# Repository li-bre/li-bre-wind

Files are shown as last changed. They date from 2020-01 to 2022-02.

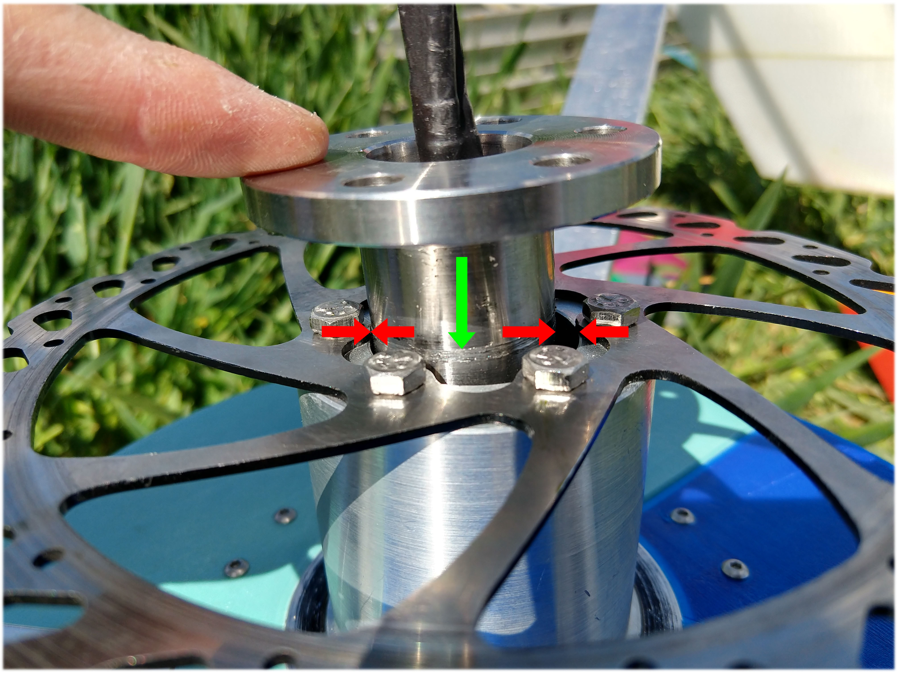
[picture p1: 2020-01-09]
05_Photos/02_Construction/01 Rotor/IMG_20190512_130845734_HDR.jpg

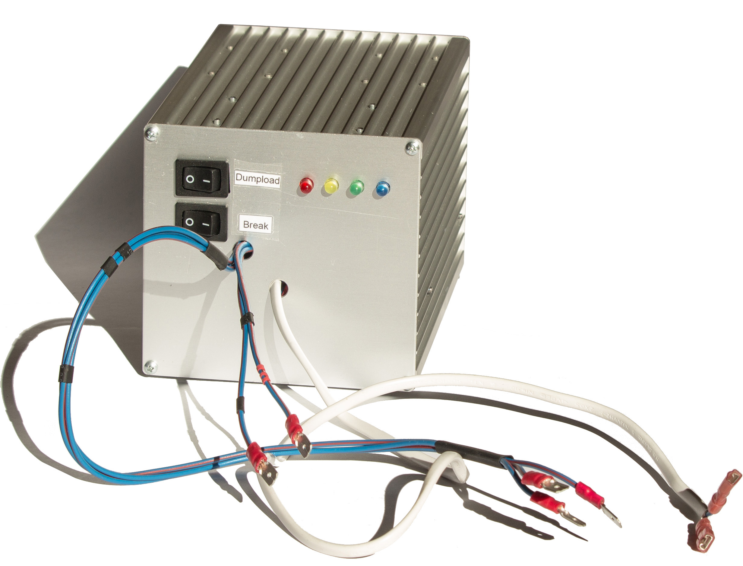
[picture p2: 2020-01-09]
05_Photos/02_Construction/02 Control/Control_Unit_closed.jpg

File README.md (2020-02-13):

# Li.Bre wind

**Li.Bre wind** is a project by [Avia Linke](https://github.com/a-linke) and [Julian Brendel](https://github.com/j-brendel) that offers an open source solution for an micro off-grid system powered by a 3D printed helical darrieus wind turbine. The project was developed as a master thesis at Technische Universität Berlin. 

## Open source micro power plant
### The development and construction of an Arduino controlled 3D printed vertical axis wind turbine

#### Abstract - English version

This master thesis describes the development, construction and testing of a prototype
version of a micro wind energy conversion system in battery charging application.
The objective of this work is to develop an open source design that enables makers
to build such a system on their own with tools and methods common in the maker
scene while using recycled material. First a concept was developed by studying the
individual subsystems and testing and simulating diﬀerent design options. Then the
ﬁnal design of the prototype was carried out. It incorporates a 3D printed helical
darrieus turbine with a swept area of equation and an electronic control unit
based on an Arduino , which facilitates diﬀerent modes of operation, among them
Maximum Power Point Tracking (MPPT) and a start-up and deceleration of the
turbine. The prototype was then manufactured and ﬁeld tests were conducted. The
turbines behavior was similar to the simulations although the measured power and
torque created by the turbine are lower than expected. A constant wind speed above equation is needed to operate the turbine. The start-up and deceleration of the
turbine were successfully tested, while MPPT could not be tested due to low wind.

#### Zusammenfassung - Deutsche Version

Diese Masterarbeit beschreibt die Entwicklung, die Konstruktion und das Testen
eines Prototypen einer Mikrowindenergieanlage zur Batterieladung. Das Ziel der
Arbeit ist die Erarbeitung eines open source Designs, das es Makern ermöglicht
selbst solch ein System zu bauen. Dabei werden Werkzeuge und Methoden verwendet,
die in der Makerszene üblich sind und wenn möglich recyceltes Material wiederver-
wertet. Zunächst wurde ein Konzept erstellt, indem die verschiedenen Teilsysteme
untersucht wurden und verschiedene Designmöglichkeiten simuliert und getestet
wurden. Anschließend wurde das ﬁnale Design des Prototypen erarbeitet. Dieses
beinhaltet einen 3D-gedruckten Helix Darrieus Rotor mit einer überstrichenen Fläche equation und eine auf einem Arduino basierende Regelungseinheit, die den
Betrieb in verschiedenen Modi ermöglicht. Dazu zählen MPPT sowie das Hochfahren
und Abbremsen des Rotors. Daraufhin wurde der Prototyp gefertigt und getestet.
Der Rotor verhält sich ähnlich wie in den Simulationen, jedoch sind die gemessenen
Leistungen und Momente niedriger als erwartet. Der Betrieb der Anlage ist ab
Wingeschwindigkeiten von über equation möglich. Das Hochfahren und Abbremsen
des Rotors wurden erfolgreich getestet, jedoch konnte der MPPT-Modus aufgrund
unzureichender Windverhälnisse nicht ausreichend getestet werden.

# Photo of Turbine

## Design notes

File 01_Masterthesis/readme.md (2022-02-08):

## Open source micro power plant - The development and construction of an Arduino controlled 3D printed vertical axis wind turbine

The PDF file of the Masterthesis can be downloaded [here](https://tubcloud.tu-berlin.de/s/zwbYHEXWewTQXEC).

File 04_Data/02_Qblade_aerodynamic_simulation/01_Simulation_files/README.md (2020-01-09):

The Qblade simulation files can be downloaded here:

[Qblade simulation v3-v9](https://tubcloud.tu-berlin.de/s/eyBzo7SFASFJWpm)

[Qblade simulation v10-v17](https://tubcloud.tu-berlin.de/s/y2Ww39XBPMs3kdm)

[Qblade simulation geometry](https://tubcloud.tu-berlin.de/s/Je3on5NNKKa9AqJ)

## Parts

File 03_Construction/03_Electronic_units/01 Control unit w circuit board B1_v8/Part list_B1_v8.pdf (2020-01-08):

Part Number Quantity | Name | Designation | Link | Sales
unit | Accessed on | Price | Cost
J1, J2 | 2
| screw terminal block | PTR AKZ500/3DS- 5.08-H | https://www.conrad.de/de/ptr-akz5003ds- 508-h-schraubklemmblock-150-mm-polzahl- 3-grau-1-st-732037.html (https://www.conrad.de/de/ptr-akz5003ds-508-h-schraubklemmblock-150-mm-polzahl-3-grau-1-st-732037.html)
1 | 10.07.2018 16:40 0.37 € | 0.74 €
J3, J4, J5, J6 | 4

screw
terminal block

PTR AKZ500/2DS-5.08-H

https://www.conrad.de/de/ptr-akz5002ds-508-h-schraubklemmblock-150-mm-polzahl-2-grau-1-st-732023.html (https://www.conrad.de/de/ptr-akz5002ds-508-h-schraubklemmblock-150-mm-polzahl-2-grau-1-st-732023.html)

1 | 10.07.2018 16:40 0.22 € | 0.88 €
RL1 - RL 3 | 3 | Relais | HJR-4102-L-12V | https://www.conrad.de/de/printrelais-12- vdc-5-a-1-wechsler-tianbo-electronics-hjr- 4102-l-12vdc-s-z-1-st-629491.html (https://www.conrad.de/de/printrelais-12-vdc-5-a-1-wechsler-tianbo-electronics-hjr-4102-l-12vdc-s-z-1-st-629491.html) | 1 | 10.07.2018 16:40 0.90 € | 2.70 €
RL4 | 1 | Relais | RT 424-12 | http://www.segor.de/#Q=RT424-12&M=1 | 1 | 10.07.2018 16:40 2.90 € | 2.90 €
D1 - D10 | 10 | Schottky-Diode SR5100

https://www.banggood.com/50pcs-SB5100-5_0A-SCHOTTKY-BARRIER-Diode-100V-5A-p-1210667.html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 (https://www.banggood.com/50pcs-SB5100-5_0A-SCHOTTKY-BARRIER-Diode-100V-5A-p-1210667.html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)

50 | 10.07.2018 16:40 | - | €
D11 | 1 | Diode | 1N4007

https://www.conrad.de/de/sigleichrichterdiode-diotec-1n4007-do-204al-1000-v-1-a-162272.html (https://www.conrad.de/de/si-gleichrichterdiode-diotec-1n4007-do-204al-1000-v-1-a-162272.html)

1 | 11.07.2018 11:22 0.08 € | 0.08 €
D12 - D 19 | 8 | Diode | 1N4148

https://www.conrad.de/de/standarddiodevishay-1n4148-tap-do-204ah-75-v-300-ma-564851.html (https://www.conrad.de/de/standarddiode-vishay-1n4148-tap-do-204ah-75-v-300-ma-564851.html)

1 | 11.07.2018 11:41 0.05 € | 0.40 €
D20 | 1 | LED | Yellow | - | €
D21 | 1 | LED | Blue | - | €
D22 | 1 | LED | Red | - | €
D23 | 1 | LED | Green | - | €
D24 | 1 | Z-Diode | BZX79C4V7

https://www.conrad.de/de/z-diodebzx79c4v7-gehaeuseart-halbleiter-do-35-onsemiconductor-zener-spannung-47-vleistung-max-ptot-500-mw-563817.html (https://www.conrad.de/de/z-diode-bzx79c4v7-gehaeuseart-halbleiter-do-35-on-semiconductor-zener-spannung-47-v-leistung-max-ptot-500-mw-563817.html)

1 | 16.07.2018 15:29 0.14 € | 0.14 €
D25 - D26 | 2 | Diode | 1N4148 | https://www.conrad.de/de/standarddiode-
| | | | vishay-1n4148-tap-do-204ah-75-v-300-ma-
| | | | 564851.html (https://www.conrad.de/de/standarddiode-vishay-1n4148-tap-do-204ah-75-v-300-ma-564851.html) | 1 | 11.07.2018 11:41 0.05 € | 0.10 €
D27, D28 | 2 | TVS-Diode | P6KE15A | http://www.segor.de/#Q=P6KE15A&M=1 | 1 | 21.08.2018 15:47 0.30 € | 0.60 €
D29 | 1 | TVS-Diode | P6KE6A8 | http://www.segor.de/#Q=P6KE6%252C8A&
| | | | M=1 (http://www.segor.de/#Q=P6KE6%252C8A&M=1) | 1 | 21.08.2018 15:47 0.30 € | 0.30 €
Q1 - Q4 | 4

n-Channel
MOSFET

IRFB4410ZPBF

https://www.conrad.de/de/mosfet-infineontechnologies-irfb4410zpbf-1-n-kanal-230-w-to-220ab-160946.html (https://www.conrad.de/de/mosfet-infineon-technologies-irfb4410zpbf-1-n-kanal-230-w-to-220ab-160946.html)

1 | 11.07.2018 14:13 0.82 € | 3.28 €
Q5 | 1

n-Channel
MOSFET | IRF710PBF

https://www.conrad.de/de/mosfet-vishayirf710pbf-1-n-kanal-36-w-to-220ab-162429.html (https://www.conrad.de/de/mosfet-vishay-irf710pbf-1-n-kanal-36-w-to-220ab-162429.html)

1 | 11.07.2018 14:16 0.28 € | 0.28 €
C1, C2 | 2

electrolytic
capacitor
200 V 820 uF | From Power Supply | - | €
C3, C4 | 2

electrolytic
capacitor

Yageo
SY035M0470B5S-1019

https://www.conrad.de/de/yageosy035m0470b5s-1019-elektrolytkondensator-radial-bedrahtet-5-mm-470-f-35-v-20-o-x-h-10-mm-x-19-mm-1-st-442613.html (https://www.conrad.de/de/yageo-sy035m0470b5s-1019-elektrolyt-kondensator-radial-bedrahtet-5-mm-470-f-35-v-20-o-x-h-10-mm-x-19-mm-1-st-442613.html)

1 | 11.07.2018 18:13 0.24 € | 0.48 €
C5 | 1

tantalum
capacitor
TA 10u-25 | http://www.segor.de/#Q=TA10u-25&M=1 | 1 | 12.07.2018 16:38 0.50 € | 0.50 €
C6 | 1

electrolytic
capacitor
33 uF | P1 | - | €
C7 | 1

electrolytic
capacitor
0.47 uF | P1 | - | €
C8, C9 | 2

ceramic
capacitor
u10-R2.5-X7R | http://www.segor.de/#Q=u10-R2.5-
| X7R&M=1 (http://www.segor.de/#Q=u10-R2.5-X7R&M=1) | 1 | 12.07.2018 16:56 0.10 € | 0.20 €
C10 | 1

electrolytic
capacitor
10 uF | P1 | - | €
C11 - C13 | 3

ceramic
capacitor

u10-R5.0-Z5U

http://www.segor.de/#Q=u10-R5.0-
Z5U&M=1 (http://www.segor.de/#Q=u10-R5.0-Z5U&M=1) | 1 | 12.07.2018 17:04 0.09 € | 0.27 €
C14 | 1

tantalum
capacitor

Tantal 4,7uF-35V RM2,5

http://www.segor.de/#Q=TA4u7-35&M=1 | 1 | 17.07.2018 13:46 0.50 € | 0.50 €
C15 | 1

ceramic
capacitor
u10-R2.5-X7R | http://www.segor.de/#Q=u10-R2.5-
X7R&M=1 (http://www.segor.de/#Q=u10-R2.5-X7R&M=1) | 1 | 12.07.2018 17:04 0.10 € | 0.10 €

F1 | 1 | Fuseholder | FKSmini- Halter/Print180° | http://www.segor.de/#Q=FKSmini-
Halter%252FPrint180%25C2%25B0&M=1 (http://www.segor.de/#Q=FKSmini-Halter%252FPrint180%25C2%25B0&M=1) | 1 | 16.07.2018 15:59 1.50 € | 1.50 €
F2 | 1 | Fuse | FKS 10A | http://www.segor.de/#Q=FKS10A%252Fmini
&M=1 (http://www.segor.de/#Q=FKS10A%252Fmini&M=1) | 1 | 16.07.2018 15:59 0.35 € | 0.35 €
U1 | 1

Voltage
Regulator 10 V LM2940T-10.0 https://www.conrad.de/de/pmicspannungsregler-linear-ldo-texasinstruments-lm2940t-100nopb-positiv-festto-220-3-1014005.html (https://www.conrad.de/de/pmic-spannungsregler-linear-ldo-texas-instruments-lm2940t-100nopb-positiv-fest-to-220-3-1014005.html)
1 | 12.07.2018 17:21 1.10 € | 1.10 €
U2 | 1 | Voltage Regulator 5 V | MC7805CT TO- 220AB | https://www.conrad.de/de/spannungsregler- linear-typ78-on-semiconductor-mc7805ct-to- 220ab-positiv-fest-5-v-1-a-175030.html (https://www.conrad.de/de/spannungsregler-linear-typ78-on-semiconductor-mc7805ct-to-220ab-positiv-fest-5-v-1-a-175030.html)
1 | 12.07.2018 16:38 0.20 € | 0.20 €
U3 | 1 | Motor Driver | JYQD_V6.3e2 | https://www.ebay.de/itm/263158812858?Vi
ewItem=&item=263158812858 | 1 | 16.07.2018 13:10 8.38 € | 8.38 €
U4, U5 | 2 | Current Sensor | ACS712 20A

https://www.ebay.de/itm/ACS712-20A-Stromsensor-Analogausgang-Current-Sensor-Hall-Sensor-Arduino/401269170566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 11001%26algo%3DREC.SEED%26ao%3D1%2 6asc%3D20160908103841%26meid%3D57e6 35c51f394274b93af9d7c8bea2ce%26pid%3D 100227%26rk%3D2%26rkt%3D6%26sd%3D1 62798921249%26itm%3D401269170566&_t rksid=p2054502.c100227.m3827 (https://www.ebay.de/itm/ACS712-20A-Stromsensor-Analogausgang-Current-Sensor-Hall-Sensor-Arduino/401269170566)

1 | 16.07.2018 15:38 2.40 € | 4.80 €
U6 | 1 | Real Time Clock DS3231 ZS042

https://www.ebay.de/itm/DS3231-ZS042-AT24C32-IIC-Modul-Precision-RTC-Echtzeituhr-Speicher-fur-Arduino/372369574177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 (https://www.ebay.de/itm/DS3231-ZS042-AT24C32-IIC-Modul-Precision-RTC-Echtzeituhr-Speicher-fur-Arduino/372369574177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)

1 | 16.07.2018 15:41 1.29 € | 1.29 €
U7 | 1 | MOSFET Driver | IR2109PBF DIP-8

https://www.conrad.de/de/pmic-gatetreiber-infineon-technologies-ir2109pbfnicht-invertierend-halbbruecke-dip-8-163094.html

1 | 16.07.2018 15:49 3.13 € | 3.13 €
U8 | 1 | Schmitt Trigger | NAND-Gate

https://www.conrad.de/de/logik-ic-gate-undinverter-texas-instruments-cd4093be-nand-gate-4000b-pdip-14-155684.html

1 | 16.07.2018 16:08 0.50 € | 0.50 €
U9 | 1

MicroSD-Card
Modul

MicroSD-Card
Modul

http://www.segor.de/#Q=MicroSD-
CardModul&M=1 | 1 | 16.07.2018 16:11 3.50 € | 3.50 €
U10 | 1 | AD-Converter | ADS1115

https://www.banggood.com/I2C-ADS1115-
16-Bit-ADC-4-Channel-Module-With-Programmable-Gain-Amplifier-For-Arduino-RPi-p-1110588.html?rmmds=search&stayold=1&cu r_warehouse=CN
1 | 16.07.2018 17:51 3.35 € | 3.35 €
SW1 | 1 | Switch | On/Off/On

https://www.conrad.de/de/wippschaltera125b11000000-250-vac-10-a-1-x-einauseinrastend0rastend-1-st-701653.html

1 | 16.07.2018 16:57 1.29 € | 1.29 €
R1 | 1

Metal Film
Resistor
1M | P3 | - | €
R2 | 1

Metal Film
Resistor
51k | P3 | - | €
R3 | 1

Metal Film
Resistor
1M | P3 | - | €
R4 | 1

Metal Film
Resistor
300k | P3 | - | €
R5 - R8 | 4 | Load Resistor | 4R

https://www.banggood.com/100W-Watt-Power-Metal-Shell-Case-Wirewound-Resistorp-89494.html?ID=49542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 (https://www.banggood.com/100W-Watt-Power-Metal-Shell-Case-Wirewound-Resistor-p-89494.html?ID=49542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)

1 | 16.07.2018 15:13 2.57 € | 10.28 €
R9 - R12 | 4

Metal Film
Resistor
200R | P3 | - | €
R13 | 1

Metal Film
Resistor
100k | P3 | - | €
R14 - R19 | 3

Metal Film
Resistor
10k | P3 | - | €

R20, R21 | 2 | Metal Film Resistor | 10R | P3 | - | €
R22, R23 | 2 | Metal Film Resistor | 100R | P3 | - | €
L1 | 1 | Inductivity | 10 A 220uF | From Power Supply | - | €
P1 | 1

electrolytic
capacitors

https://www.banggood.com/200pcs-0_1-220uF-15-Value-Electrolytic-Capacitor-Assortment-Box-Kit-p-1032358.html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 (https://www.banggood.com/200pcs-0_1-220uF-15-Value-Electrolytic-Capacitor-Assortment-Box-Kit-p-1032358.html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)

1 | 12.07.2018 16:45 3.76 € | 3.76 €
P2 | 10

pin row strip
male

https://www.banggood.com/10-Pcs-40-Pin-2_54mm-Single-Row-Male-Pin-Header-Strip-For-Arduino-p-918427.html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 (https://www.banggood.com/10-Pcs-40-Pin-2_54mm-Single-Row-Male-Pin-Header-Strip-For-Arduino-p-918427.html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)

10 | 10.07.2018 16:40 3.42 € | 3.42 €
P3 | 1 | Resistor Pack | metal film resistor

https://www.banggood.com/de/300Pcs-1-14W-Metal-Film-Resistor-Resistance-30-Values-Assortment-Kit-p-1091920.html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 (https://www.banggood.com/de/300Pcs-1-14W-Metal-Film-Resistor-Resistance-30-Values-Assortment-Kit-p-1091920.html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)

1 | 16.07.2018 15:29 2.32 € | 2.32 €
P4 | 1 | LED-Pack | 100 Pcs 3MM 5 Colors

https://www.banggood.com/100Pcs-20Ma-F3-3MM-5Colors-Ultra-Bright-LED-Diode-p-966102.html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 (https://www.banggood.com/100Pcs-20Ma-F3-3MM-5Colors-Ultra-Bright-LED-Diode-p-966102.html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)

1 | 16.07.2018 15:33 1.74 € | 1.74 €
1 | Arduino Mega | Mega2560

https://www.banggood.com/Mega2560-R3-ATmega2560-16AU-Control-Board-With-USB-Cable-For-Arduino-p-73020.html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 (https://www.banggood.com/Mega2560-R3-ATmega2560-16AU-Control-Board-With-USB-Cable-For-Arduino-p-73020.html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)

1 | 16.07.2018 15:35 9.03 € | 9.03 €
1 | Anemometer

for WS1080 und
WS3080

https://www.elv.at/ersatz-anemometer-fuerdie-funk-wetterstation-ws1080-undws3080.html (https://www.elv.at/ersatz-anemometer-fuer-die-funk-wetterstation-ws1080-und-ws3080.html)

1 | 16.07.2018 15:44 9.95 € | 9.95 €

1

4 GB micro SD
Card

https://www.conrad.de/de/transcendpremium-microsdhc-karte-4-gb-class-10-416524.html (https://www.conrad.de/de/transcend-premium-microsdhc-karte-4-gb-class-10-416524.html)

| 1 | 16.07.2018 18:02 6.69 € | 6.69 €

1

Thermal
Compound

http://www.segor.de/#Q=WLP05-
Tube&M=1 (http://www.segor.de/#Q=WLP05-Tube&M=1) | 1 | 16.07.2018 18:02 1.50 € | 1.50 €
| | | 92.53 €

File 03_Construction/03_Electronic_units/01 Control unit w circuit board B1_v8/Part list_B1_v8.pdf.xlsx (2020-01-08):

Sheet: Overview
 | Overview
 |  |  |  |  |  |  | 2019-07-03
 | Part Number | Quantity | Name | Designation | Link | Sales unit | Accessed on | Price | Cost | To buy | Had alternative
 | J1, J2 | 2 | screw terminal block | PTR AKZ500/3DS-5.08-H | https://www.conrad.de/de/ptr-akz5003ds-508-h-schraubklemmblock-150-mm-polzahl-3-grau-1-st-732037.html | 1 | 2018-07-10 | 0.37 € | 0.74 € | X
 | J3, J4, J5, J6 | 4 | screw terminal block | PTR AKZ500/2DS-5.08-H | https://www.conrad.de/de/ptr-akz5002ds-508-h-schraubklemmblock-150-mm-polzahl-2-grau-1-st-732023.html | 1 | 2018-07-10 | 0.22 € | 0.88 € | X
 |  |  |  |  |  |  |  |  | 0.00 €
 |  |  |  |  |  |  |  |  | 0.00 €
 |  |  |  |  |  |  |  |  | 0.00 €
 |  |  |  |  |  |  |  |  | 0.00 €
 | RL1 - RL 3 | 3 | Relais | HJR-4102-L-12V-S-Z | https://www.conrad.de/de/printrelais-12-vdc-5-a-1-wechsler-tianbo-electronics-hjr-4102-l-12vdc-s-z-1-st-629491.html | 1 | 2018-07-10 | 0.90 € | 2.70 €
 | RL4 | 1 | Relais | RT 424-12 | http://www.segor.de/#Q=RT424-12&M=1 | 1 | 2018-07-10 | 2.90 € | 2.90 € | X
 |  |  |  |  |  |  |  |  | 0.00 €
 |  |  |  |  |  |  |  |  | 0.00 €
 |  |  |  |  |  |  |  |  | 0.00 €
 | D1 - D10 | 10 | Schottky-Diode | SR5100 | https://www.banggood.com/50pcs-SB5100-5_0A-SCHOTTKY-BARRIER-Diode-100V-5A-p-1210667.html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 | 50 | 2018-07-10 |  | 0.00 € | X | https://www.conrad.de/de/schottky-diode-gleichrichter-tru-components-tc-sb5100-do-201-100-v-einzeln-1582136.html
 | D11 | 1 | Diode | 1N4007 | https://www.conrad.de/de/si-gleichrichterdiode-diotec-1n4007-do-204al-1000-v-1-a-162272.html | 1 | 2018-07-11 | 0.08 € | 0.08 €
 | D12 - D 19 | 8 | Diode | 1N4148 | https://www.conrad.de/de/standarddiode-vishay-1n4148-tap-do-204ah-75-v-300-ma-564851.html | 1 | 2018-07-11 | 0.05 € | 0.40 €
 | D20 | 1 | LED | Yellow |  |  |  |  | 0.00 €
 | D21 | 1 | LED | Blue |  |  |  |  | 0.00 €
 | D22 | 1 | LED | Red |  |  |  |  | 0.00 €
 | D23 | 1 | LED | Green |  |  |  |  | 0.00 €
 | D24 | 1 | Z-Diode | BZX79C4V7 | https://www.conrad.de/de/z-diode-bzx79c4v7-gehaeuseart-halbleiter-do-35-on-semiconductor-zener-spannung-47-v-leistung-max-ptot-500-mw-563817.html | 1 | 2018-07-16 | 0.14 € | 0.14 €
 | D25 - D26 | 2 | Diode | 1N4148 | https://www.conrad.de/de/standarddiode-vishay-1n4148-tap-do-204ah-75-v-300-ma-564851.html | 1 | 2018-07-11 | 0.05 € | 0.10 €
 | D27, D28 | 2 | TVS-Diode | P6KE15A | http://www.segor.de/#Q=P6KE15A&M=1 | 1 | 2018-08-21 | 0.30 € | 0.60 €
 | D29 | 1 | TVS-Diode | P6KE6A8 | http://www.segor.de/#Q=P6KE6%252C8A&M=1 | 1 | 2018-08-21 | 0.30 € | 0.30 €
 |  |  |  |  |  |  |  |  | 0.00 €
 |  |  |  |  |  |  |  |  | 0.00 €
 | Q1 - Q4 | 4 | n-Channel MOSFET | IRFB4410ZPBF | https://www.conrad.de/de/mosfet-infineon-technologies-irfb4410zpbf-1-n-kanal-230-w-to-220ab-160946.html | 1 | 2018-07-11 | 0.82 € | 3.28 €
 | Q5 | 1 | n-Channel MOSFET | IRF710PBF | https://www.conrad.de/de/mosfet-vishay-irf710pbf-1-n-kanal-36-w-to-220ab-162429.html | 1 | 2018-07-11 | 0.28 € | 0.28 € |  | NMOS IRFU310
 |  |  |  |  |  |  |  |  | 0.00 €
 |  |  |  |  |  |  |  |  | 0.00 €
 | C1, C2 | 2 | electrolytic capacitor | Teapo LXK 200 V, 820 uF | From Power Supply |  |  |  | 0.00 €
 | C3, C4 | 2 | electrolytic capacitor | Yageo SY035M0470B5S-1019 | https://www.conrad.de/de/yageo-sy035m0470b5s-1019-elektrolyt-kondensator-radial-bedrahtet-5-mm-470-f-35-v-20-o-x-h-10-mm-x-19-mm-1-st-442613.html | 1 | 2018-07-11 | 0.24 € | 0.48 € | X
 | C5 | 1 | tantalum capacitor | TA 10u-25 | http://www.segor.de/#Q=TA10u-25&M=1 | 1 | 2018-07-12 | 0.50 € | 0.50 € | X
 | C6 | 1 | electrolytic capacitor | 33 uF | P1 |  |  |  | 0.00 €
 | C7 | 1 | electrolytic capacitor | 0.47 uF | P1 |  |  |  | 0.00 €
 | C8, C9 | 2 | ceramic capacitor | u10-R2.5-X7R | http://www.segor.de/#Q=u10-R2.5-X7R&M=1 | 1 | 2018-07-12 | 0.10 € | 0.20 € | X
 | C10 | 1 | electrolytic capacitor | 10 uF | P1 |  |  |  | 0.00 €
 |  |  |  |  |  |  |  |  | 0.00 €
 | C11 - C13 | 3 | ceramic capacitor | u10-R5.0-Z5U | http://www.segor.de/#Q=u10-R5.0-Z5U&M=1 | 1 | 2018-07-12 | 0.09 € | 0.27 €
 | C14 | 1 | tantalum capacitor | Tantal 4,7uF-35V RM2,5 | http://www.segor.de/#Q=TA4u7-35&M=1 | 1 | 2018-07-17 | 0.50 € | 0.50 €
 | C15 | 1 | ceramic capacitor | u10-R2.5-X7R | http://www.segor.de/#Q=u10-R2.5-X7R&M=1 | 1 | 2018-07-12 | 0.10 € | 0.10 €
 |  |  |  |  |  |  |  |  | 0.00 €
 |  |  |  |  |  |  |  |  | 0.00 €
 | F1 | 1 | Fuseholder | FKSmini-Halter/Print180° | http://www.segor.de/#Q=FKSmini-Halter%252FPrint180%25C2%25B0&M=1 | 1 | 2018-07-16 | 1.50 € | 1.50 €
 | F2 | 1 | Fuse | FKS 10A | http://www.segor.de/#Q=FKS10A%252Fmini&M=1 | 1 | 2018-07-16 | 0.35 € | 0.35 €
 |  |  |  |  |  |  |  |  | 0.00 €
 | U1 | 1 | Voltage Regulator 10 V | LM2940T-10.0 | https://www.conrad.de/de/pmic-spannungsregler-linear-ldo-texas-instruments-lm2940t-100nopb-positiv-fest-to-220-3-1014005.html | 1 | 2018-07-12 | 1.10 € | 1.10 €
 | U2 | 1 | Voltage Regulator 5 V | MC7805CT TO-220AB | https://www.conrad.de/de/spannungsregler-linear-typ78-on-semiconductor-mc7805ct-to-220ab-positiv-fest-5-v-1-a-175030.html | 1 | 2018-07-12 | 0.20 € | 0.20 € | X
 | U3 | 1 | Motor Driver | JYQD_V6.3e2 | https://www.ebay.de/itm/263158812858?ViewItem=&item=263158812858 | 1 | 2018-07-16 | 8.38 € | 8.38 €
 | U4, U5 | 2 | Current Sensor | ACS712 20A | https://www.ebay.de/itm/ACS712-20A-Stromsensor-Analogausgang-Current-Sensor-Hall-Sensor-Arduino/401269170566 | 1 | 2018-07-16 | 2.40 € | 4.80 €
 | U6 | 1 | Real Time Clock | DS3231 ZS042 | https://www.ebay.de/itm/DS3231-ZS042-AT24C32-IIC-Modul-Precision-RTC-Echtzeituhr-Speicher-fur-Arduino/372369574177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 | 1 | 2018-07-16 | 1.29 € | 1.29 €
 | U7 | 1 | MOSFET Driver | IR2109PBF DIP-8 | https://www.conrad.de/de/pmic-gate-treiber-infineon-technologies-ir2109pbf-nicht-invertierend-halbbruecke-dip-8-163094.html | 1 | 2018-07-16 | 3.13 € | 3.13 €
 | U8 | 1 | Schmitt Trigger | NAND-Gate | https://www.conrad.de/de/logik-ic-gate-und-inverter-texas-instruments-cd4093be-nand-gate-4000b-pdip-14-155684.html | 1 | 2018-07-16 | 0.50 € | 0.50 €
 | U9 | 1 | MicroSD-Card Modul | MicroSD-Card Modul | http://www.segor.de/#Q=MicroSD-CardModul&M=1 | 1 | 2018-07-16 | 3.50 € | 3.50 €
 | U10 | 1 | AD-Converter | ADS1115 | https://www.banggood.com/I2C-ADS1115-16-Bit-ADC-4-Channel-Module-With-Programmable-Gain-Amplifier-For-Arduino-RPi-p-1110588.html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 | 1 | 2018-07-16 | 3.35 € | 3.35 €
 |  |  |  |  |  |  |  |  | 0.00 €
 |  |  |  |  |  |  |  |  | 0.00 €
 |  |  |  |  |  |  |  |  | 0.00 €
 | SW1 | 1 | Switch | On/Off/On | https://www.conrad.de/de/wippschalter-a125b11000000-250-vac-10-a-1-x-einausein-rastend0rastend-1-st-701653.html | 1 | 2018-07-16 | 1.29 € | 1.29 € | x
 |  |  |  |  |  |  |  |  | 0.00 €
 | R1 | 1 | Metal Film Resistor | 1M | P3 |  |  |  | 0.00 €
 | R2 | 1 | Metal Film Resistor | 51k | P3 |  |  |  | 0.00 €
 | R3 | 1 | Metal Film Resistor | 1M | P3 |  |  |  | 0.00 €
 | R4 | 1 | Metal Film Resistor | 300k | P3 |  |  |  | 0.00 €
 | R5 - R8 | 4 | Load Resistor | 4R | https://www.banggood.com/100W-Watt-Power-Metal-Shell-Case-Wirewound-Resistor-p-89494.html?ID=49542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 | 1 | 2018-07-16 | 2.57 € | 10.28 €
 | R9 - R12 | 4 | Metal Film Resistor | 200R | P3 |  |  |  | 0.00 €
 | R13 | 1 | Metal Film Resistor | 100k | P3 |  |  |  | 0.00 €
 | R14 - R19 | 3 | Metal Film Resistor | 10k | P3 |  |  |  | 0.00 €
 | R20, R21 | 2 | Metal Film Resistor | 10R | P3 |  |  |  | 0.00 €
 | R22, R23 | 2 | Metal Film Resistor | 100R | P3
 |  |  |  |  |  |  |  |  | 0.00 €
 |  |  |  |  |  |  |  |  | 0.00 €
 | L1 | 1 | Inductivity | 10 A 220uF | From Power Supply |  |  |  | 0.00 €
 |  |  |  |  |  |  |  |  | 0.00 €
 |  |  |  |  |  |  |  |  | 0.00 €
 |  |  |  |  |  |  |  |  | 0.00 €
Packs | P1 | 1 | electrolytic capacitors |  | https://www.banggood.com/200pcs-0_1-220uF-15-Value-Electrolytic-Capacitor-Assortment-Box-Kit-p-1032358.html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 | 1 | 2018-07-12 | 3.76 € | 3.76 €
 | P2 | 10 | pin strip male |  | https://www.banggood.com/10-Pcs-40-Pin-2_54mm-Single-Row-Male-Pin-Header-Strip-For-Arduino-p-918427.html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 | 10 | 2018-07-10 | 3.42 € | 3.42 €
 | P3 | 1 | Resistor Pack | metal film resistor | https://www.banggood.com/de/300Pcs-1-14W-Metal-Film-Resistor-Resistance-30-Values-Assortment-Kit-p-1091920.html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 | 1 | 2018-07-16 | 2.32 € | 2.32 €
 | P4 | 1 | LED-Pack | 100 Pcs 3MM 5 Colors | https://www.banggood.com/100Pcs-20Ma-F3-3MM-5Colors-Ultra-Bright-LED-Diode-p-966102.html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 | 1 | 2018-07-16 | 1.74 € | 1.74 €
 |  |  |  |  |  |  |  |  | 0.00 €
Other |  | 1 | Arduino Mega | Mega2560 | https://www.banggood.com/Mega2560-R3-ATmega2560-16AU-Control-Board-With-USB-Cable-For-Arduino-p-73020.html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 | 1 | 2018-07-16 | 9.03 € | 9.03 €
 |  | 1 | Anemometer | for WS1080 und WS3080 | https://www.elv.at/ersatz-anemometer-fuer-die-funk-wetterstation-ws1080-und-ws3080.html | 1 | 2018-07-16 | 9.95 € | 9.95 €
 |  | 1 | 4 GB micro SD Card |  | https://www.conrad.de/de/transcend-premium-microsdhc-karte-4-gb-class-10-416524.html | 1 | 2018-07-16 | 6.69 € | 6.69 €
 |  | 1 | Thermal Compound |  | http://www.segor.de/#Q=WLP05-Tube&M=1 | 1 | 2018-07-16 | 1.50 € | 1.50 € | X
 |  | 1 | Prototyping Circuit Board | TRU COMPONENTS SU527769 | https://www.conrad.de/de/tru-components-su527769-europlatine-hartpapier-l-x-b-160-mm-x-100-mm-35-m-rastermass-254-mm-inhalt-1-st-1570681.html | 1 | 2019-02-22 | 3.69 € | 3.69 €
 |  | 1 | Copper wire | 10 m silver coated | http://www.segor.de/#Q=S1%252C0(25m)&M=1 | 1 | 2019-02-25 | 9.90 € | 9.90 €
 |  | 1 | Housing | Proma 130048 Universal-Housing 168 x 110 x 104 | https://www.conrad.de/de/proma-130048-universal-gehaeuse-168-x-110-x-104-aluminium-aluminium-1-st-522970.html | 1 | 2019-02-25 | 30.99 € | 30.99 €
 |  | 1 | Thermal conductive pad | 100 mm x 100 mm x 1 mm | http://www.segor.de/#Q=W%25C3%25A4rmeleitkissen100x100&M=1 | 1 | 2019-02-25 | 6.40 € | 6.40 €
 |  | 20 | Jumper wire | 20cm Male - Female | https://www.amazon.de/Female-Female-Male-Female-Male-Male-Steckbr%C3%BCcken-Drahtbr%C3%BCcken-bunt/dp/B01EV70C78 | 20 | 2019-02-25 | 5.94 € | 5.94 €
 |  | 1 | Box with crimp spade connectors |  | https://www.amazon.de/dp/B06WP7TZY2/ref=pe_1941441_77686091_tnp_email_TE_Cardp_1?th=1 | 1 | 2019-02-25 | 16.99 € | 16.99 €
 |  |  |  |  |  |  |  |  | 166.44 €
 |  |  |  |  |  |  |  |  | 0

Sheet: Overview zur abgabe
Part Number | Quantity | Name | Designation | Link | Sales unit | Accessed on | Price | Cost
J1, J2 | 2 | Screw terminal block | PTR AKZ500/3DS-5.08-H | https://www.conrad.de/de/ptr-akz5003ds-508-h-schraubklemmblock-150-mm-polzahl-3-grau-1-st-732037.html | 1 | 2018-07-10 16:40 | 0.37 € | 0.74 €
J3, J4, J5, J6 | 4 | Screw terminal block | PTR AKZ500/2DS-5.08-H | https://www.conrad.de/de/ptr-akz5002ds-508-h-schraubklemmblock-150-mm-polzahl-2-grau-1-st-732023.html | 1 | 2018-07-10 16:40 | 0.22 € | 0.88 €
RL1 - RL 3 | 3 | Relais | HJR-4102-L-12V | https://www.conrad.de/de/printrelais-12-vdc-5-a-1-wechsler-tianbo-electronics-hjr-4102-l-12vdc-s-z-1-st-629491.html | 1 | 2018-07-10 16:40 | 0.90 € | 2.70 €
RL4 | 1 | Relais | RT 424-12 | http://www.segor.de/#Q=RT424-12&M=1 | 1 | 2018-07-10 16:40 | 2.90 € | 2.90 €
D1 - D10 | 10 | Schottky-diode | SR5100 | https://www.banggood.com/50pcs-SB5100-5_0A-SCHOTTKY-BARRIER-Diode-100V-5A-p-1210667.html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 | 50 | 2018-07-10 16:40 |  | 0.00 €
D11 | 1 | Diode | 1N4007 | https://www.conrad.de/de/si-gleichrichterdiode-diotec-1n4007-do-204al-1000-v-1-a-162272.html | 1 | 2018-07-11 11:22 | 0.08 € | 0.08 €
D12 - D 19 | 8 | Diode | 1N4148 | https://www.conrad.de/de/standarddiode-vishay-1n4148-tap-do-204ah-75-v-300-ma-564851.html | 1 | 2018-07-11 11:41 | 0.05 € | 0.40 €
D20 | 1 | LED | Yellow |  |  |  |  | 0.00 €
D21 | 1 | LED | Blue |  |  |  |  | 0.00 €
D22 | 1 | LED | Red |  |  |  |  | 0.00 €
D23 | 1 | LED | Green |  |  |  |  | 0.00 €
D24 | 1 | Z-diode | BZX79C4V7 | https://www.conrad.de/de/z-diode-bzx79c4v7-gehaeuseart-halbleiter-do-35-on-semiconductor-zener-spannung-47-v-leistung-max-ptot-500-mw-563817.html | 1 | 2018-07-16 15:29 | 0.14 € | 0.14 €
D25 - D26 | 2 | Diode | 1N4148 | https://www.conrad.de/de/standarddiode-vishay-1n4148-tap-do-204ah-75-v-300-ma-564851.html | 1 | 2018-07-11 11:41 | 0.05 € | 0.10 €
D27, D28 | 2 | TVS-diode | P6KE15A | http://www.segor.de/#Q=P6KE15A&M=1 | 1 | 2018-08-21 15:47 | 0.30 € | 0.60 €
D29 | 1 | TVS-diode | P6KE6A8 | http://www.segor.de/#Q=P6KE6%252C8A&M=1 | 1 | 2018-08-21 15:47 | 0.30 € | 0.30 €
Q1 - Q4 | 4 | N-channel MOSFET | IRFB4410ZPBF | https://www.conrad.de/de/mosfet-infineon-technologies-irfb4410zpbf-1-n-kanal-230-w-to-220ab-160946.html | 1 | 2018-07-11 14:13 | 0.82 € | 3.28 €
Q5 | 1 | N-channel MOSFET | IRF710PBF | https://www.conrad.de/de/mosfet-vishay-irf710pbf-1-n-kanal-36-w-to-220ab-162429.html | 1 | 2018-07-11 14:16 | 0.28 € | 0.28 €
C1, C2 | 2 | Electrolytic capacitor | 200 V 820 uF | From Power Supply |  |  |  | 0.00 €
C3, C4 | 2 | Electrolytic capacitor | Yageo SY035M0470B5S-1019 | https://www.conrad.de/de/yageo-sy035m0470b5s-1019-elektrolyt-kondensator-radial-bedrahtet-5-mm-470-f-35-v-20-o-x-h-10-mm-x-19-mm-1-st-442613.html | 1 | 2018-07-11 18:13 | 0.24 € | 0.48 €
C5 | 1 | Tantalum capacitor | TA 10u-25 | http://www.segor.de/#Q=TA10u-25&M=1 | 1 | 2018-07-12 16:38 | 0.50 € | 0.50 €
C6 | 1 | Electrolytic capacitor | 33 uF | P1 |  |  |  | 0.00 €
C7 | 1 | Electrolytic capacitor | 0.47 uF | P1 |  |  |  | 0.00 €
C8, C9 | 2 | Ceramic capacitor | u10-R2.5-X7R | http://www.segor.de/#Q=u10-R2.5-X7R&M=1 | 1 | 2018-07-12 16:56 | 0.10 € | 0.20 €
C10 | 1 | Electrolytic capacitor | 10 uF | P1 |  |  |  | 0.00 €
C11 - C13 | 3 | Ceramic capacitor | u10-R5.0-Z5U | http://www.segor.de/#Q=u10-R5.0-Z5U&M=1 | 1 | 2018-07-12 17:04 | 0.09 € | 0.27 €
C14 | 1 | Tantalum capacitor | Tantal 4,7uF-35V RM2,5 | http://www.segor.de/#Q=TA4u7-35&M=1 | 1 | 2018-07-17 13:46 | 0.50 € | 0.50 €
C15 | 1 | Tantalum capacitor | u10-R2.5-X7R | http://www.segor.de/#Q=u10-R2.5-X7R&M=1 | 1 | 2018-07-12 17:04 | 0.10 € | 0.10 €
F1 | 1 | Fuseholder | FKSmini-Halter/Print180° | http://www.segor.de/#Q=FKSmini-Halter%252FPrint180%25C2%25B0&M=1 | 1 | 2018-07-16 15:59 | 1.50 € | 1.50 €
F2 | 1 | Fuse | FKS 10A | http://www.segor.de/#Q=FKS10A%252Fmini&M=1 | 1 | 2018-07-16 15:59 | 0.35 € | 0.35 €
U1 | 1 | Voltage regulator 10 V | LM2940T-10.0 | https://www.conrad.de/de/pmic-spannungsregler-linear-ldo-texas-instruments-lm2940t-100nopb-positiv-fest-to-220-3-1014005.html | 1 | 2018-07-12 17:21 | 1.10 € | 1.10 €
U2 | 1 | Voltage regulator 5 V | MC7805CT TO-220AB | https://www.conrad.de/de/spannungsregler-linear-typ78-on-semiconductor-mc7805ct-to-220ab-positiv-fest-5-v-1-a-175030.html | 1 | 2018-07-12 16:38 | 0.20 € | 0.20 €
U3 | 1 | Motor driver | JYQD_V6.3e2 | https://www.ebay.de/itm/263158812858?ViewItem=&item=263158812858 | 1 | 2018-07-16 13:10 | 8.38 € | 8.38 €
U4, U5 | 2 | Current sensor | ACS712 20A | https://www.ebay.de/itm/ACS712-20A-Stromsensor-Analogausgang-Current-Sensor-Hall-Sensor-Arduino/401269170566 | 1 | 2018-07-16 15:38 | 2.40 € | 4.80 €
U6 | 1 | Real time clock | DS3231 ZS042 | https://www.ebay.de/itm/DS3231-ZS042-AT24C32-IIC-Modul-Precision-RTC-Echtzeituhr-Speicher-fur-Arduino/372369574177 | 1 | 2018-07-16 15:41 | 1.29 € | 1.29 €
U7 | 1 | MOSFET driver | IR2109PBF DIP-8 | https://www.conrad.de/de/pmic-gate-treiber-infineon-technologies-ir2109pbf-nicht-invertierend-halbbruecke-dip-8-163094.html | 1 | 2018-07-16 15:49 | 3.13 € | 3.13 €
U8 | 1 | Schmitt trigger | NAND-Gate | https://www.conrad.de/de/logik-ic-gate-und-inverter-texas-instruments-cd4093be-nand-gate-4000b-pdip-14-155684.html | 1 | 2018-07-16 16:08 | 0.50 € | 0.50 €
U9 | 1 | MicroSD-card modul | MicroSD-Card Modul | http://www.segor.de/#Q=MicroSD-CardModul&M=1 | 1 | 2018-07-16 16:11 | 3.50 € | 3.50 €
U10 | 1 | AD-converter | ADS1115 | https://www.banggood.com/I2C-ADS1115-16-Bit-ADC-4-Channel-Module-With-Programmable-Gain-Amplifier-For-Arduino-RPi-p-1110588.html | 1 | 2018-07-16 17:51 | 3.35 € | 3.35 €
SW1 | 1 | Switch | On/Off/On | https://www.conrad.de/de/wippschalter-a125b11000000-250-vac-10-a-1-x-einausein-rastend0rastend-1-st-701653.html | 1 | 2018-07-16 16:57 | 1.29 € | 1.29 €
R1 | 1 | Metal film resistor | 1M | P3 |  |  |  | 0.00 €
R2 | 1 | Metal film resistor | 51k | P3 |  |  |  | 0.00 €
R3 | 1 | Metal film resistor | 1M | P3 |  |  |  | 0.00 €
R4 | 1 | Metal film resistor | 300k | P3 |  |  |  | 0.00 €
R5 - R8 | 4 | Power resistor | 4R | https://www.banggood.com/100W-Watt-Power-Metal-Shell-Case-Wirewound-Resistor-p-89494.html | 1 | 2018-07-16 15:13 | 2.57 € | 10.28 €
R9 - R12 | 4 | Metal film resistor | 200R | P3 |  |  |  | 0.00 €
R13 | 1 | Metal film resistor | 100k | P3 |  |  |  | 0.00 €
R14 - R19 | 3 | Metal film resistor | 10k | P3 |  |  |  | 0.00 €
R20, R21 | 2 | Metal film resistor | 10R | P3 |  |  |  | 0.00 €
R22, R23 | 2 | Metal film resistor | 100R | P3 |  |  |  | 0.00 €
L1 | 1 | Inductivity | 10 A 220uF | From Power Supply |  |  |  | 0.00 €
P1 | 1 | Electrolytic capacitors |  | https://www.banggood.com/200pcs-0_1-220uF-15-Value-Electrolytic-Capacitor-Assortment-Box-Kit-p-1032358.html | 1 | 2018-07-12 16:45 | 3.76 € | 3.76 €
P2 | 10 | Pin row strip male |  | https://www.banggood.com/10-Pcs-40-Pin-2_54mm-Single-Row-Male-Pin-Header-Strip-For-Arduino-p-918427.html | 10 | 2018-07-10 16:40 | 3.42 € | 3.42 €
P3 | 1 | Resistor pack | metal film resistor | https://www.banggood.com/de/300Pcs-1-14W-Metal-Film-Resistor-Resistance-30-Values-Assortment-Kit-p-1091920.html | 1 | 2018-07-16 15:29 | 2.32 € | 2.32 €
P4 | 1 | LED-pack | 100 Pcs 3MM 5 Colors | https://www.banggood.com/100Pcs-20Ma-F3-3MM-5Colors-Ultra-Bright-LED-Diode-p-966102.html | 1 | 2018-07-16 15:33 | 1.74 € | 1.74 €
 | 1 | Arduino MEGA | Mega2560 | https://www.banggood.com/Geekcreit-MEGA-2560-R3-ATmega2560-MEGA2560-Development-Board-With-USB-Cable-For-Arduino-p-73020.html | 1 | 2018-07-16 15:35 | 9.03 € | 9.03 €
 | 1 | Anemometer | for WS1080 und WS3080 | https://www.elv.at/ersatz-anemometer-fuer-die-funk-wetterstation-ws1080-und-ws3080.html | 1 | 2018-07-16 15:44 | 9.95 € | 9.95 €
 | 1 | 4 GB micro SD card |  | https://www.conrad.de/de/transcend-premium-microsdhc-karte-4-gb-class-10-416524.html | 1 | 2018-07-16 18:02 | 6.69 € | 6.69 €
 | 1 | Thermal compound |  | http://www.segor.de/#Q=WLP05-Tube&M=1 | 1 | 2018-07-16 18:02 | 1.50 € | 1.50 €
 | 1 | Prototyping Circuit Board | TRU COMPONENTS SU527769 | https://www.conrad.de/de/tru-components-su527769-europlatine-hartpapier-l-x-b-160-mm-x-100-mm-35-m-rastermass-254-mm-inhalt-1-st-1570681.html | 1 | 2019-02-22 15:50 | 3.69 € | 3.69 €
 | 1 | Copper wire | 10 m silver coated | http://www.segor.de/#Q=S1%252C0(25m)&M=1 | 1 | 2019-02-25 11:58 | 9.90 € | 9.90 €
 | 1 | Housing | Proma 130048 Universal-Housing 168 x 110 x 104 | https://www.conrad.de/de/proma-130048-universal-gehaeuse-168-x-110-x-104-aluminium-aluminium-1-st-522970.html | 1 | 2019-02-25 11:58 | 30.99 € | 30.99 €
 | 1 | Thermal conductive pad | 100 mm x 100 mm x 1 mm | http://www.segor.de/#Q=W%25C3%25A4rmeleitkissen100x100&M=1 | 1 | 2019-02-25 11:58 | 6.40 € | 6.40 €
 | 20 | Jumper wire | 20cm Male - Female | https://www.amazon.de/Female-Female-Male-Female-Male-Male-Steckbr%C3%BCcken-Drahtbr%C3%BCcken-bunt/dp/B01EV70C78/ | 20 | 2019-02-25 11:58 | 5.94 € | 5.94 €
 | 1 | Box with crimp spade connectors |  | https://www.amazon.de/dp/B06WP7TZY2/ref=pe_1941441_77686091_tnp_email_TE_Cardp_1?th=1 | 1 | 2019-02-25 11:58 | 16.99 € | 16.99 €
 |  |  |  |  |  |  |  | 166.44 €

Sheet: DCDC-Direkt
Spule | Mantikala p60 & p106ff
Anforderungen
Induktivität [uH] | 200
I_max [A] | 10
P_loss_Max [W] | 2
-> R_DC MAX [Ohm|mOhm] | 0.0200 | 20.00
Induktivität
Worst Case Low Power -> High Inductivity
Vorgabe r
P | 10 |  | I_OUT | 0.77
V_OUT | 13 |  | I_L = I_DC | 0.77
V_IN | 35 |  | D | 0.37
r | 2 |  | T [us] | 31.87
f | 31373 |  | L[uH] (Mantikala) | 169.30
 |  |  | I_AC | 1.22
 |  |  | I_PK | 1.99
 |  |  | I_AG | 0.65
Worst Case High Power - > High Currents
Vorgabe r
P | 100 |  | V_ON | 48.00
V_OUT | 12 |  | V_OFF | 12.00
V_IN | 60 |  | I_OUT | 8.33
L [uH] | 200 |  | I_L = I_DC | 8.33
f | 31373 |  | D | 0.20
 |  |  | T [us] | 31.87
 |  |  | r | 0.18
 |  |  | I_AC | 0.76
 |  |  | I_PK | 9.10
 |  |  | I_AG | 0.66
Bei 10 W soll Continuous conduction Mode erreicht werden -> r=2 (bei V_in = 35V (aus erster messreihe) und V_OUT 13 V (Voller Akku schwacher Ladestrom) -> 170 uH
Mit gleicher Spule (mit Sicherheit 200 uH) maximale Stromstärke bei grosßer Leistung -> 100 W macht 9,1 A I_PK
Leitungswiderstand
rho [(Ω·mm2)/m] | 0.017
l [m] | 1
A [mm^2] | 0.7853981634
R [Ohm|mOhm] | 0.02164507226 | 21.64507226
P_loss @ 10 A [W] | 2.164507226
Für REVERSE BOOST MODE
Vorgabe L
P | 112.7489194 |  | V_ON | 12.00
V_OUT | 36 |  | V_OFF | 24.00
V_IN | 12 |  | I_OUT | 3.13
L [uH] | 211 |  | I_L = I_DC | 9.40
f | 31373 |  | D | 0.67
 |  |  | T [us] | 31.87
 |  |  | r | 0.13 | 0.128623505
 |  |  | I_AC | 0.60
 |  |  | I_PK | 10.00
 |  |  | I_AG | 0.17
Maximal 103 W um bei I_PK von 10A zu bleiben. IDEAL! Wirkungsgrad = 100 %
Wenn V_IN größer I_PK entsprechend kleiner, trotzdem 100W max!!
Spule Mantikala p.107ff
P | 100 |  | I_O = I_L [A] | 8.33
V_O | 12 |  | D | 0.21
V_D | 0.7 |  | t_on [us] | 6.68
V_IN | 60 |  | V_ON | 47.94
V_SW | 0.06 |  | Et [V us] | 320.03
f | 31373 |  | L * I [uh A] | 1600.13
r | 0.2 |  | L [uH] | 192.02
 |  |  | I_PK [A] | 9.17
DCDC Diode
Keine Diode mehr, dafür Halbbrücke mit 2 MOSFETs
OUT Kondensator
Anforderungen:
Ripple Current[I] | 0.48
V_OUT_max (15 V + 50%) [V] | 22.5
I_RMS_OUT [A] (max) | 0.48
ESR (siehe Bsp Datenblatt) [Ohm]
V_RIPPLE_RMS_IN [V|%] |  |  |  |  |  | https://www.conrad.de/de/elektrolyt-kondensator-radial-bedrahtet-5-mm-1000-f-25-vdc-20-o-x-h-10-mm-x-20-mm-vishay-2222-037-36102-1-st-446132.html
 |  |  |  |  |  | http://www.produktinfo.conrad.com/datenblaetter/425000-449999/446132-da-01-en-STANDARD_ELKO_85GRAD_1000__25V.pdf
Auswahl
2 * 50 V,220 uF (von Avias Dad, hatte ich noch)
=IN Kondensator Für Rev. BOOST MODE
Anforderungen:
Ripple Current[I] | 1.94
V_max (15 V + 50%) | 22.5
V_RIPPLE_IN_MAX (5-10% * V_IN) | 0.91
I_RMS_IN [A] (max) | 1.94
ESR (siehe Bsp Datenblatt) [Ohm] | 0.40
V_RIPPLE_RMS_IN [V|%] | 0.78 | 0.003677194783
Worst @ D=50
Vorgabe L
P | 100 |  | V_ON | 13.00
V_OUT | 26.0 |  | V_OFF | 12.99
V_IN | 13 |  | I_OUT | 3.85
L [uH] | 211 |  | I_L = I_DC | 7.69
f | 31373 |  | D | 0.50
 |  |  | T [us] | 31.87
 |  |  | r | 0.13
 |  |  | I_AC | 0.49
 |  |  | I_PK | 8.18
 |  |  | I_AG | 0.22
Die von Avias Dad rechen nicht wg. Ripple Current im reverse Betrieb. Entweder 4 parallel oder größere
z.B. 2 x Yageo SY025M0470B5S-1015 | https://www.conrad.de/de/elektrolyt-kondensator-radial-bedrahtet-5-mm-470-f-25-v-20-o-x-h-10-mm-x-15-mm-yageo-sy025m0470b5s-1015-1-st-442625.html
 | Preis: 2 x 0,18 €
IN Kondensator
Anforderungen:
Ripple Current[I] | 4.19
V_max (60 V + 50%) | 90
V_RIPPLE_IN_MAX (5-10% * V_IN) | 1.68
I_RMS_IN [A] (max) | 4.19
ESR (siehe Bsp Datenblatt) [Ohm] | 0.40
V_RIPPLE_RMS_IN [V|%] | 1.68 | 0.07
Worst @ D=50
Vorgabe L
P | 100 |  | V_ON | 12.00
V_OUT | 12 |  | V_OFF | 12.00
V_IN | 24 |  | I_OUT | 8.33
L [uH] | 200 |  | I_L = I_DC | 8.33
f | 31373 |  | D | 0.50
 |  |  | T [us] | 31.87
 |  |  | r | 0.11 |  | Kostet 2-5 €
 |  |  | I_AC | 0.48 |  | https://www.conrad.de/de/elektrolyt-kondensatoren-o0245812.html?tfo_ATT_NOMINAL_VOLTAGE=200%20V
 |  |  | I_PK | 8.81
 |  |  | I_AG | 0.42
 |  |  |  |  |  |  | Teapo LXK 820uF 200V 25x50 2.25A
Auswahl:
2 Große Eingangs Kondensatoren aus Netzteil: 200 V 680 uF
=OUT Kondensator Für Rev. BOOST MODE
I_RMS_OUT [A] (max) | 4.55
 | die ausgewählten müssten rechen (2 x 3,45 A = 6,9 A)
worst Case @ D=50
Vorgabe L
P | 100 |  | V_ON | 11.00
V_OUT | 22 |  | V_OFF | 11.00
V_IN | 11 |  | I_OUT | 4.55
L [uH] | 211 |  | I_L = I_DC | 9.09
f | 31373 |  | D | 0.50
 |  |  | T [us] | 31.87
 |  |  | r | 0.09
 |  |  | I_AC | 0.42
 |  |  | I_PK | 9.51
 |  |  | I_AG | 0.18

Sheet: Treiber
Auswahl Treiber-IC
Anforderung: | V_IN_HIGH | 1…3,3V
 | Konfig | High Side
 | V_CC | 9-12V
 | Preis | max 2 €
Möglich:
 | Spalte1 | Konfiguration | V_IH | V_CC | t_r | t_f | I_O + | DT | Preis | Bemerkung | Wo
 | IR2011 | High and Low | 2.2 | 10 … 20 | 35 | 20 | 1000 | - | 2.50 €
 | IR2101 | High and Low | 3 | 10 … 20 | 100 | 50 | 130 | - | 1.80 €
 | IR2102 | High and Low | 3 | 10 … 20 | 100 | 50 | 130 | - | 0.83 €
 | IR2104 | Half Bridge | 3 | 10 … 20 | 100 | 50 | 130 | 520 | 2.04 € |  | Segor
 | IR2106 | High and Low | 2.9 | 10 … 20 | 150 | 50 | 120 | - | 1.80 €
 | IR2109 | Half Bridge | 2.9 | 10 … 20 | 150 | 50 | 120 | 540 | 1.92 € |  | C | <-
 | IR2125 | Current limiting High | 2.2 | 0 … 18 | 43 | 26 | 1000 | - | 5.30 €
 | IR2127 | Current sensing High | 3 | 10 … 20 | 80 | 40 | 200 | - | 2.43 € |  | C
 | IR2184 | Half Bridge | 2.7 | 10 … 20 | 40 | 20 | 1900 | 400 | 2.70 € |  | Segor
 | IR2301 | High and Low | 2.9 | 5 … 20 | 130 | 50 | 120 | - | 2.48 €
 | IRS2181 | High and Low | 2.5 | 10 … 20 | 40 | 20 | 2000 | - | 2.65 € |  | Segor
Fragen
2153/55: Self Oszilating?
Deadtime (Halfbridge)
 |  |  | Berechnet
f | 62000 | hz
T | 1.612903226e-05 | s
T | 16129.03226 | ns
Anteil DT | 0.1%
DT | 16.12903226 | ns | X
DT | 520 | ns
Anteil DT | 3.2% |  | X
Beschluss: Zu viele Fehlerquellen und zu kompliziert -> Schottky Diode

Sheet: Bootstrap Comp
Kondensator
Anforderungen | C | >=150nF
 | Material | non Elko, low ESR
NMOS | IRFB4110PBF
Q_G [nC|C] | 150 | 1.5e-07
I_qbs [uA|A] | 75 | 7.5e-05
Q_is [nC|C] | 5 | 5e-09
I_Cbs | 0 |  | not Elko
f [Hz] | 32000
V_CC [V] | 10
V_f [V] | 0.7
V_LS [V] | 0.7 |  | DCDC-Diode?
V_Min [V] | 1 |  | Annahme???
C [nf|F] | 80.87993421 | 8.087993421e-08
Bemerkungen:
DT 04 4 p2 | paralleling electrolytic and low ESR ceramic may result in an efficient solution
AN 978 p5 | Local decoupling capacitors on the V CC (and digital) supply are useful in practice to compensate for the inductance of the supply lines.
Auswahl | 2x 100nF Keramik (104) parallel
Diode
Anforderungen | V_F | minimal
 | V_RRM | min 100 V
 | I_F [mA|A] | 4.8 | 0.0048 | f*Q_G
 | Diode | V_RRM [V] | I_F [mA] | V_F [V] @25°C, 10mA | Hab ich
 | BAT 46 | 100 | 5000 | 0,45 @25°C, 10mA
 | SB5100 | 100 | 150 | < 0,79 @25°C, 5A | x

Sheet: MOSFET
MOSFET Auswahl
Anforderung | R_DS_ON | max 10 mOhm
 | Preis | max 2 €
 | V_DS | min 100V
 | Ausführung | N-Kanal
 | Montage | Lochdurchführung
Such-Link Conrad: | https://www.conrad.de/de/mosfets-o5104021.html?tfo_ATT_MOUNTING_METHOD=Durchf%C3%BChrungsloch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
Auswahl | IRFB4410ZPBF

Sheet: Sonstige
Spannungsregler
Anforderungen
 | V_in_min | 12 V
 | V_OUT | 10 V
 | I_OUT | 1 A
LM2940SX-10/NOPB
https://www.conrad.de/de/pmic-spannungsregler-linear-ldo-texas-instruments-lm2940sx-10nopb-positiv-fest-to-263-3-1014000.html
Gleichrichter-Dioden
Anforderungen
I_max | 3,5 A
U_max | 100 V
V_F | min
switching speed | fast
Auswahl:
SB5100
I_max [A] | 5
U_max | 100 V
V_F | 0,75 V
switching speed | fast
Sicherungen
Halter: | FKSmini-Halter/Print180° |  | bei Segor | 1.50 €
Sicherung: | FKS 10A/mini |  |  | 0.35 €
Shunt-Widerstände
30mR-2W-5% /-10x
Kabelanschlüsse
Schraubklemmen 2 polig, 3 polig
http://www.segor.de/#Q=ARK2-HUT&M=1
http://www.segor.de/#Q=ARK3-HUT&M=1
Strommesssensoren
ACS
Relais
zum Umschalten der 3 Motorphasen von Motor auf Generatorbetrieb <->
Anforderungen
I_max [A] | 5
U_max [V/AC] | 100
U_DC_schalt [V] | 12
Arduino hat nur 20 mA pro Pin am Augang, also gerade genug. Lieber gleichzeitig mit MOSFET schalten.
Printrelais 12 V/DC 5 A 1 Wechsler Tianbo Electronics HJR-4102-L-12VDC-S-Z
https://www.conrad.de/de/printrelais-12-vdc-5-a-1-wechsler-tianbo-electronics-hjr-4102-l-12vdc-s-z-1-st-629491.html
zum Zu/Abschalten der Versorgung des Motorcontrollers beim Umschalten von Motor auf Generatorbetrieb <->
Anforderungen
I_max [A] | 8
U_max [V/DC] | 60
U_DC_schalt [V] | 12
P_max [W] | 100
https://produktinfo.conrad.com/datenblaetter/500000-524999/505439-da-01-de-LEISTUNGSRELAIS_12V.pdf
Alternativ:
http://www.farnell.com/datasheets/1504641.pdf |  |  |  | aber kein RM 2.52
http://www.segor.de/#Q=F3611-12&M=1
Alternative 2
http://www.segor.de/#Q=G6D1A-12VDC&M=1
https://www.mouser.de/datasheet/2/307/en-g6d-23247.pdf |  |  |  |  | hat RM 2.54, max 5 A @ 20V DC, max 30 V DC
Alternative 3 - sehr gut
http://www.segor.de/#Q=RT424-12&M=1
C:\Users\J B\tubcloud\Module\Masterarbeit\Elektro\Datenblätter\Relais RT 424 12V_com.pdf |  |  |  |  |  | 2 Wechsler in serie: 60V DC @ 8 A

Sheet: Dumpload
Der Dumpload soll in der Lage sein mit 10 A Strom die gesamte Nennleistung des Motors in Wärme umzuwandeln, das entspricht 350 W / 10 A = 35 V -> 35 V / 10 A = 3,5 Ohm
Dazu werden 4 100 W Lastwiderstände als 2 in Reihe und 2 Parallel verschalten. Das ergibt 4 Ohm also bei 37,4 V werden mit 9,35 A 350 W verbraucht. Frage: Wie schnell dreht er sich dann?
Schaltung
C:\Users\J B\tubcloud\Module\Masterarbeit\Literatur\Elektro\MOSFET\P_channel MOSFETs high side - Vishay.pdf
N_Channel:
Anforderungen:
U_GS_th=LL (5 V max)
IRFU310
P_Channel:
Anforderung: V_DS=100 V, I_max=10 A
https://www.conrad.de/de/mosfet-infineon-technologies-irf9540npbf-1-p-kanal-140-w-to-220-162537.html
R_DS_on= 114mR
https://www.conrad.de/de/mosfet-infineon-technologies-irf9530npbf-1-p-kanal-79-w-to-220-162536.html
R_DS_on= 200mR

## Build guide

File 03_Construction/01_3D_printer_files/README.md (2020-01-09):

The 3D printer files can be downloaded here:

[01 Rotor Blades](https://tubcloud.tu-berlin.de/s/gkeiq44S942ZKe3)

[02 Adapter to Ansmann Generator](https://tubcloud.tu-berlin.de/s/N5EZWiJLEPLzEFw)

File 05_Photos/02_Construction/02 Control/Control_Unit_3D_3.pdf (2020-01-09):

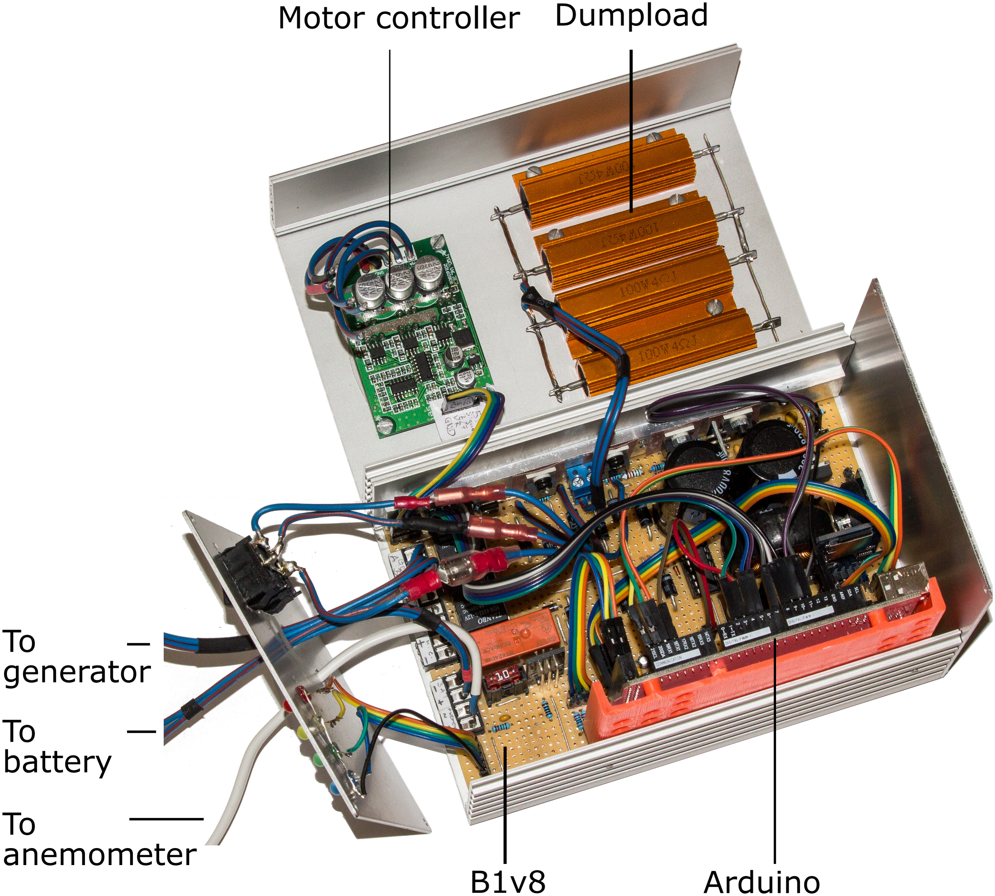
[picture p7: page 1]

Motor controller Dumpload

B1v8 | Arduino

To
generator
To
battery
To
anemometer

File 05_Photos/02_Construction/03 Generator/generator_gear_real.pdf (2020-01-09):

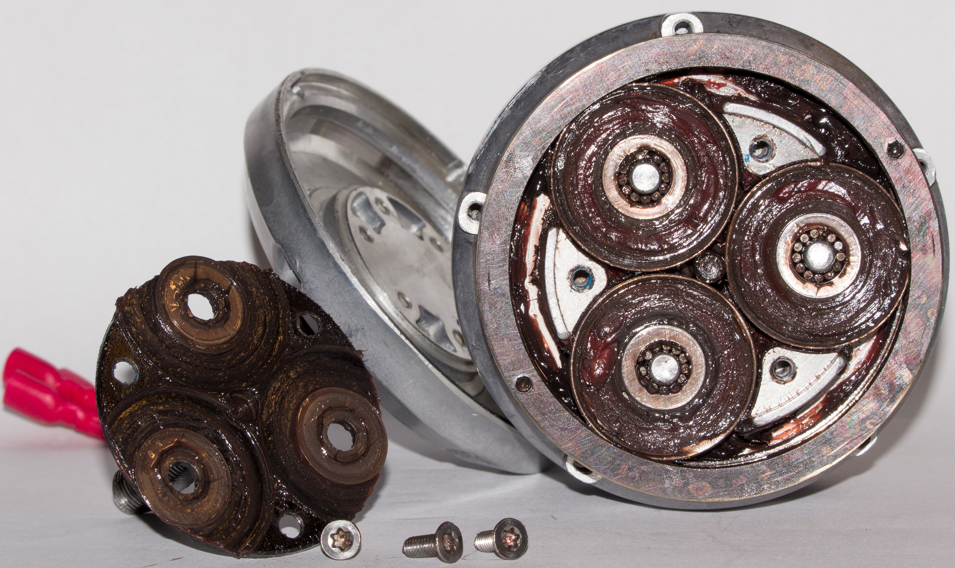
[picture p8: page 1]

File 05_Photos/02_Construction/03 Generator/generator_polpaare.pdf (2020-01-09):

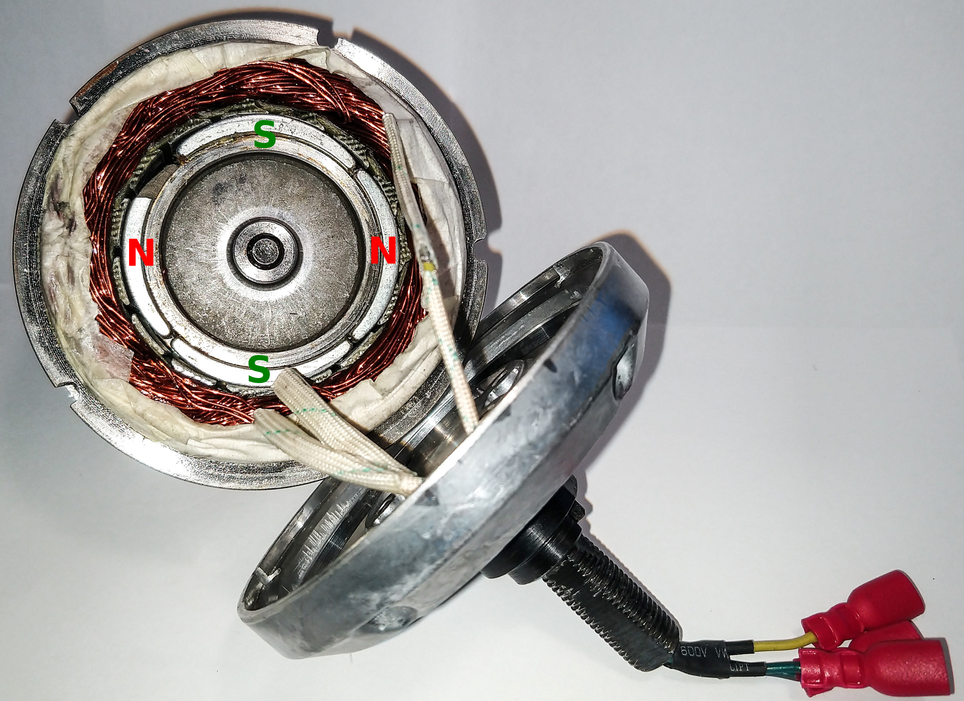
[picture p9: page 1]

SS

N

N

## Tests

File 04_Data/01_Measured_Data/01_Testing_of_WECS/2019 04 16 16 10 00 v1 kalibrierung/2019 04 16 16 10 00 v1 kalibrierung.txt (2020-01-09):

Hour Minute Second RPM v1 RPM_ct wind_ct
 27
15 35 20 0 5.94 0 27
15 35 23 0 5.94 0 27
15 35 26 0 5.94 0 29
15 35 29 0 6.38 0 27
15 35 32 0 5.94 0 29
15 35 35 0 6.38 0 35
15 35 38 0 7.70 0 33
15 35 41 0 7.26 0 28
15 35 44 0 6.16 0 21
15 35 47 0 4.62 0 19
15 35 50 0 4.18 0 21
15 35 53 0 4.62 0 19
15 35 56 0 4.18 0 18
15 35 59 0 3.96 0 18
15 36 2 0 3.96 0 16
15 36 5 0 3.52 0 15
15 36 8 0 3.30 0 14
15 36 11 0 3.08 0 15
15 36 14 0 3.30 0 15
15 36 17 0 3.30 0 16
15 36 20 0 3.52 0 13
15 36 23 0 2.86 0 12
15 36 26 0 2.64 0 14
15 36 29 0 3.08 0 10
15 36 32 0 2.20 0 13
15 36 35 0 2.86 0 18
15 36 38 0 3.96 0 27
15 36 41 0 5.94 0 26
15 36 44 0 5.72 0 22
15 36 47 0 4.84 0 18
15 36 50 0 3.96 0 19
15 36 53 0 4.18 0 20
15 36 56 0 4.40 0 18
15 36 59 0 3.96 0 16
15 37 2 0 3.52 0 15
15 37 5 0 3.30 0 16
15 37 8 0 3.52 0 13
15 37 11 0 2.86 0 25
15 37 14 0 5.50 0 16
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

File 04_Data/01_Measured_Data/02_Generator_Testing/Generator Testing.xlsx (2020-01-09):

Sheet: Messungen
allgemeine Werte:
 | Generatorumfang (Seilauflage) [m]: |  |  |  |  | Messwiderstand Kurzschluss [Ohm]:
 | 0.322 |  |  |  |  | 0.03 |  |  |  |  |  | U=R*I
 | Generatorradius (Seilauflage) [m]: |  |  |  |  |  |  |  |  |  |  |  |  |  |  |  |  |  |  |  |  |  |  |  | 0.7166666667
 | 0.051 |  |  |  |  |  |  |  |  |  |  |  |  |  |  |  |  |  |  |  |  |  | 0.3676470588
Generator
 |  | Bohrmaschine
Last | Messdatum: | Gang: | Drehzahlstufe: | Drehzahl [rpm]: | Drehzahl MW [Hz]: | Drehzahl StA [Hz]: | Gewicht MW [kg] | Gewicht StA [kg] | max. Gewicht [kg] | max Drehmoment [Nm] | Drehmoment [Nm] | Spannung MW [V]: | Spannung StAb [V]: | Strom MW [A]: | Strom StA [V]: | Antriebsleis [W]: | Aufnleis MW [W]: | Aufnleis StA [W]: | Abgabeleistung [W]: | Eingangsleistung Bat [W] | Drehzahl 1 [Hz]: | Drehzahl 2 [Hz]: | Drehzahl 3 [Hz]: | Drehzahl 4 [Hz]: | Drehzahl 5 [Hz]: | Drehzahl 6 [Hz]: | Drehzahl 7 [Hz]: | Drehzahl 8 [Hz]: | Drehzahl 9 [Hz]: | Gewicht 1 [kg]: | Gewicht 2 [kg]: | Gewicht 3 [kg]: | Gewicht 4 [kg]: | Gewicht 5 [kg]: | Gewicht 6 [kg]: | Gewicht 7 [kg]: | Gewicht 8 [kg]: | Gewicht 9 [kg]: | Gewicht 10 [kg]: | U1 | U2 | U3 | U4 | U5 | U6 | U7 | U8 | U9 | U10 | U11
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

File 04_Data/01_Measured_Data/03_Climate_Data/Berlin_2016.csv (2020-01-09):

Stationname | Date | UnitOfHeight | sensorHeightAboveGround | Latitude | Longitude | StationHeight | geoQualityLevel | windspeed | UnitOfWindspeed | windspeedQualityLevel | winddirection | UnitOfWinddirection | windrichtungQualityLevel
Berlin-Tempelhof | 2016-01-01T00:00:00Z | m | 10 | 52.467488 | 13.402115 | 48 | certain | 1.4 | m/sec | high | 170 | degrees | high
Berlin-Tempelhof | 2016-01-01T01:00:00Z | m | 10 | 52.467488 | 13.402115 | 48 | certain | 1.4 | m/sec | high | 180 | degrees | high
Berlin-Tempelhof | 2016-01-01T02:00:00Z | m | 10 | 52.467488 | 13.402115 | 48 | certain | 1.5 | m/sec | high | 210 | degrees | high
Berlin-Tempelhof | 2016-01-01T03:00:00Z | m | 10 | 52.467488 | 13.402115 | 48 | certain | 1.5 | m/sec | high | 220 | degrees | high
Berlin-Tempelhof | 2016-01-01T04:00:00Z | m | 10 | 52.467488 | 13.402115 | 48 | certain | 1.5 | m/sec | high | 230 | degrees | high
Berlin-Tempelhof | 2016-01-01T05:00:00Z | m | 10 | 52.467488 | 13.402115 | 48 | certain | 1.7 | m/sec | high | 240 | degrees | high
Berlin-Tempelhof | 2016-01-01T06:00:00Z | m | 10 | 52.467488 | 13.402115 | 48 | certain | 1.1 | m/sec | high | 220 | degrees | high
Berlin-Tempelhof | 2016-01-01T07:00:00Z | m | 10 | 52.467488 | 13.402115 | 48 | certain | 0.9 | m/sec | high | 200 | degrees | high
Berlin-Tempelhof | 2016-01-01T08:00:00Z | m | 10 | 52.467488 | 13.402115 | 48 | certain | 2.2 | m/sec | high | 230 | degrees | high
Berlin-Tempelhof | 2016-01-01T09:00:00Z | m | 10 | 52.467488 | 13.402115 | 48 | certain | 2.6 | m/sec | high | 230 | degrees | high
Berlin-Tempelhof | 2016-01-01T10:00:00Z | m | 10 | 52.467488 | 13.402115 | 48 | certain | 2.4 | m/sec | high | 220 | degrees | high
Berlin-Tempelhof | 2016-01-01T11:00:00Z | m | 10 | 52.467488 | 13.402115 | 48 | certain | 2.3 | m/sec | high | 230 | degrees | high
Berlin-Tempelhof | 2016-01-01T12:00:00Z | m | 10 | 52.467488 | 13.402115 | 48 | certain | 1.9 | m/sec | high | 240 | degrees | high
Berlin-Tempelhof | 2016-01-01T13:00:00Z | m | 10 | 52.467488 | 13.402115 | 48 | certain | 1.6 | m/sec | high | 230 | degrees | high
Berlin-Tempelhof | 2016-01-01T14:00:00Z | m | 10 | 52.467488 | 13.402115 | 48 | certain | 1.6 | m/sec | high | 250 | degrees | high
Berlin-Tempelhof | 2016-01-01T15:00:00Z | m | 10 | 52.467488 | 13.402115 | 48 | certain | 1.6 | m/sec | high | 240 | degrees | high
Berlin-Tempelhof | 2016-01-01T16:00:00Z | m | 10 | 52.467488 | 13.402115 | 48 | certain | 1.8 | m/sec | high | 220 | degrees | high
Berlin-Tempelhof | 2016-01-01T17:00:00Z | m | 10 | 52.467488 | 13.402115 | 48 | certain | 1.5 | m/sec | high | 210 | degrees | high
Berlin-Tempelhof | 2016-01-01T18:00:00Z | m | 10 | 52.467488 | 13.402115 | 48 | certain | 1.2 | m/sec | high | 190 | degrees | high
Berlin-Tempelhof | 2016-01-01T19:00:00Z | m | 10 | 52.467488 | 13.402115 | 48 | certain | 1.2 | m/sec | high | 150 | degrees | high
Berlin-Tempelhof | 2016-01-01T20:00:00Z | m | 10 | 52.467488 | 13.402115 | 48 | certain | 0.7 | m/sec | high | 240 | degrees | high
Berlin-Tempelhof | 2016-01-01T21:00:00Z | m | 10 | 52.467488 | 13.402115 | 48 | certain | 1.2 | m/sec | high | 130 | degrees | high
Berlin-Tempelhof | 2016-01-01T22:00:00Z | m | 10 | 52.467488 | 13.402115 | 48 | certain | 0.9 | m/sec | high | 130 | degrees | high
Berlin-Tempelhof | 2016-01-01T23:00:00Z | m | 10 | 52.467488 | 13.402115 | 48 | certain | 1.9 | m/sec | high | 90 | degrees | high
Berlin-Tempelhof | 2016-01-02T00:00:00Z | m | 10 | 52.467488 | 13.402115 | 48 | certain | 2.1 | m/sec | high | 80 | degrees | high
Berlin-Tempelhof | 2016-01-02T01:00:00Z | m | 10 | 52.467488 | 13.402115 | 48 | certain | 3.1 | m/sec | high | 70 | degrees | high
Berlin-Tempelhof | 2016-01-02T02:00:00Z | m | 10 | 52.467488 | 13.402115 | 48 | certain | 3.5 | m/sec | high | 80 | degrees | high
Berlin-Tempelhof | 2016-01-02T03:00:00Z | m | 10 | 52.467488 | 13.402115 | 48 | certain | 3.3 | m/sec | high | 80 | degrees | high
Berlin-Tempelhof | 2016-01-02T04:00:00Z | m | 10 | 52.467488 | 13.402115 | 48 | certain | 3.4 | m/sec | high | 90 | degrees | high
Berlin-Tempelhof | 2016-01-02T05:00:00Z | m | 10 | 52.467488 | 13.402115 | 48 | certain | 3.6 | m/sec | high | 90 | degrees | high
Berlin-Tempelhof | 2016-01-02T06:00:00Z | m | 10 | 52.467488 | 13.402115 | 48 | certain | 4.8 | m/sec | high | 90 | degrees | high
Berlin-Tempelhof | 2016-01-02T07:00:00Z | m | 10 | 52.467488 | 13.402115 | 48 | certain | 5.4 | m/sec | high | 80 | degrees | high
Berlin-Tempelhof | 2016-01-02T08:00:00Z | m | 10 | 52.467488 | 13.402115 | 48 | certain | 6.3 | m/sec | high | 80 | degrees | high
Berlin-Tempelhof | 2016-01-02T09:00:00Z | m | 10 | 52.467488 | 13.402115 | 48 | certain | 6.9 | m/sec | high | 80 | degrees | high
Berlin-Tempelhof | 2016-01-02T10:00:00Z | m | 10 | 52.467488 | 13.402115 | 48 | certain | 5.9 | m/sec | high | 80 | degrees | high
Berlin-Tempelhof | 2016-01-02T11:00:00Z | m | 10 | 52.467488 | 13.402115 | 48 | certain | 6.4 | m/sec | high | 90 | degrees | high
Berlin-Tempelhof | 2016-01-02T12:00:00Z | m | 10 | 52.467488 | 13.402115 | 48 | certain | 6.2 | m/sec | high | 100 | degrees | high
Berlin-Tempelhof | 2016-01-02T13:00:00Z | m | 10 | 52.467488 | 13.402115 | 48 | certain | 6.4 | m/sec | high | 90 | degrees | high
Berlin-Tempelhof | 2016-01-02T14:00:00Z | m | 10 | 52.467488 | 13.402115 | 48 | certain | 7.5 | m/sec | high | 90 | degrees | high
Berlin-Tempelhof | 2016-01-02T15:00:00Z | m | 10 | 52.467488 | 13.402115 | 48 | certain | 7.7 | m/sec | high | 90 | degrees | high
Berlin-Tempelhof | 2016-01-02T16:00:00Z | m | 10 | 52.467488 | 13.402115 | 48 | certain | 8.3 | m/sec | high | 90 | degrees | high
Berlin-Tempelhof | 2016-01-02T17:00:00Z | m | 10 | 52.467488 | 13.402115 | 48 | certain | 7.3 | m/sec | high | 100 | degrees | high
Berlin-Tempelhof | 2016-01-02T18:00:00Z | m | 10 | 52.467488 | 13.402115 | 48 | certain | 7.5 | m/sec | high | 110 | degrees | high
Berlin-Tempelhof | 2016-01-02T19:00:00Z | m | 10 | 52.467488 | 13.402115 | 48 | certain | 7.8 | m/sec | high | 110 | degrees | high
Berlin-Tempelhof | 2016-01-02T20:00:00Z | m | 10 | 52.467488 | 13.402115 | 48 | certain | 7.7 | m/sec | high | 110 | degrees | high
Berlin-Tempelhof | 2016-01-02T21:00:00Z | m | 10 | 52.467488 | 13.402115 | 48 | certain | 7.4 | m/sec | high | 110 | degrees | high
Berlin-Tempelhof | 2016-01-02T22:00:00Z | m | 10 | 52.467488 | 13.402115 | 48 | certain | 7.4 | m/sec | high | 110 | degrees | high
Berlin-Tempelhof | 2016-01-02T23:00:00Z | m | 10 | 52.467488 | 13.402115 | 48 | certain | 7.8 | m/sec | high | 100 | degrees | high
Berlin-Tempelhof | 2016-01-03T00:00:00Z | m | 10 | 52.467488 | 13.402115 | 48 | certain | 7.6 | m/sec | high | 100 | degrees | high
Berlin-Tempelhof | 2016-01-03T01:00:00Z | m | 10 | 52.467488 | 13.402115 | 48 | certain | 6.9 | m/sec | high | 100 | degrees | high
Berlin-Tempelhof | 2016-01-03T02:00:00Z | m | 10 | 52.467488 | 13.402115 | 48 | certain | 6.4 | m/sec | high | 110 | degrees | high
Berlin-Tempelhof | 2016-01-03T03:00:00Z | m | 10 | 52.467488 | 13.402115 | 48 | certain | 6.8 | m/sec | high | 110 | degrees | high
Berlin-Tempelhof | 2016-01-03T04:00:00Z | m | 10 | 52.467488 | 13.402115 | 48 | certain | 6.6 | m/sec | high | 110 | degrees | high
Berlin-Tempelhof | 2016-01-03T05:00:00Z | m | 10 | 52.467488 | 13.402115 | 48 | certain | 7 | m/sec | high | 100 | degrees | high
Berlin-Tempelhof | 2016-01-03T06:00:00Z | m | 10 | 52.467488 | 13.402115 | 48 | certain | 5.8 | m/sec | high | 100 | degrees | high
Berlin-Tempelhof | 2016-01-03T07:00:00Z | m | 10 | 52.467488 | 13.402115 | 48 | certain | 5.5 | m/sec | high | 100 | degrees | high
Berlin-Tempelhof | 2016-01-03T08:00:00Z | m | 10 | 52.467488 | 13.402115 | 48 | certain | 5.8 | m/sec | high | 110 | degrees | high
Berlin-Tempelhof | 2016-01-03T09:00:00Z | m | 10 | 52.467488 | 13.402115 | 48 | certain | 6.2 | m/sec | high | 110 | degrees | high
Berlin-Tempelhof | 2016-01-03T10:00:00Z | m | 10 | 52.467488 | 13.402115 | 48 | certain | 5.9 | m/sec | high | 100 | degrees | high
Berlin-Tempelhof | 2016-01-03T11:00:00Z | m | 10 | 52.467488 | 13.402115 | 48 | certain | 5.9 | m/sec | high | 100 | degrees | high
Berlin-Tempelhof | 2016-01-03T12:00:00Z | m | 10 | 52.467488 | 13.402115 | 48 | certain | 5.8 | m/sec | high | 100 | degrees | high
Berlin-Tempelhof | 2016-01-03T13:00:00Z | m | 10 | 52.467488 | 13.402115 | 48 | certain | 5.1 | m/sec | high | 110 | degrees | high
Berlin-Tempelhof | 2016-01-03T14:00:00Z | m | 10 | 52.467488 | 13.402115 | 48 | certain | 5.5 | m/sec | high | 110 | degrees | high
Berlin-Tempelhof | 2016-01-03T15:00:00Z | m | 10 | 52.467488 | 13.402115 | 48 | certain | 5.8 | m/sec | high | 100 | degrees | high
Berlin-Tempelhof | 2016-01-03T16:00:00Z | m | 10 | 52.467488 | 13.402115 | 48 | certain | 4.9 | m/sec | high | 110 | degrees | high
Berlin-Tempelhof | 2016-01-03T17:00:00Z | m | 10 | 52.467488 | 13.402115 | 48 | certain | 6.2 | m/sec | high | 110 | degrees | high
Berlin-Tempelhof | 2016-01-03T18:00:00Z | m | 10 | 52.467488 | 13.402115 | 48 | certain | 6.4 | m/sec | high | 110 | degrees | high
Berlin-Tempelhof | 2016-01-03T19:00:00Z | m | 10 | 52.467488 | 13.402115 | 48 | certain | 6 | m/sec | high | 110 | degrees | high
Berlin-Tempelhof | 2016-01-03T20:00:00Z | m | 10 | 52.467488 | 13.402115 | 48 | certain | 5.1 | m/sec | high | 110 | degrees | high
Berlin-Tempelhof | 2016-01-03T21:00:00Z | m | 10 | 52.467488 | 13.402115 | 48 | certain | 4.9 | m/sec | high | 110 | degrees | high
Berlin-Tempelhof | 2016-01-03T22:00:00Z | m | 10 | 52.467488 | 13.402115 | 48 | certain | 4.1 | m/sec | high | 100 | degrees | high
Berlin-Tempelhof | 2016-01-03T23:00:00Z | m | 10 | 52.467488 | 13.402115 | 48 | certain | 4.3 | m/sec | high | 110 | degrees | high
Berlin-Tempelhof | 2016-01-04T00:00:00Z | m | 10 | 52.467488 | 13.402115 | 48 | certain | 4.6 | m/sec | high | 110 | degrees | high
Berlin-Tempelhof | 2016-01-04T01:00:00Z | m | 10 | 52.467488 | 13.402115 | 48 | certain | 4.7 | m/sec | high | 110 | degrees | high
Berlin-Tempelhof | 2016-01-04T02:00:00Z | m | 10 | 52.467488 | 13.402115 | 48 | certain | 4 | m/sec | high | 100 | degrees | high
Berlin-Tempelhof | 2016-01-04T03:00:00Z | m | 10 | 52.467488 | 13.402115 | 48 | certain | 4.3 | m/sec | high | 100 | degrees | high
Berlin-Tempelhof | 2016-01-04T04:00:00Z | m | 10 | 52.467488 | 13.402115 | 48 | certain | 5.9 | m/sec | high | 100 | degrees | high
Berlin-Tempelhof | 2016-01-04T05:00:00Z | m | 10 | 52.467488 | 13.402115 | 48 | certain | 5.2 | m/sec | high | 100 | degrees | high
Berlin-Tempelhof | 2016-01-04T06:00:00Z | m | 10 | 52.467488 | 13.402115 | 48 | certain | 5.8 | m/sec | high | 90 | degrees | high
Berlin-Tempelhof | 2016-01-04T07:00:00Z | m | 10 | 52.467488 | 13.402115 | 48 | certain | 5.5 | m/sec | high | 90 | degrees | high
Berlin-Tempelhof | 2016-01-04T08:00:00Z | m | 10 | 52.467488 | 13.402115 | 48 | certain | 5.6 | m/sec | high | 90 | degrees | high
Berlin-Tempelhof | 2016-01-04T09:00:00Z | m | 10 | 52.467488 | 13.402115 | 48 | certain | 5.3 | m/sec | high | 80 | degrees | high
Berlin-Tempelhof | 2016-01-04T10:00:00Z | m | 10 | 52.467488 | 13.402115 | 48 | certain | 5.1 | m/sec | high | 90 | degrees | high
Berlin-Tempelhof | 2016-01-04T11:00:00Z | m | 10 | 52.467488 | 13.402115 | 48 | certain | 5.1 | m/sec | high | 100 | degrees | high
Berlin-Tempelhof | 2016-01-04T12:00:00Z | m | 10 | 52.467488 | 13.402115 | 48 | certain | 4.8 | m/sec | high | 90 | degrees | high
Berlin-Tempelhof | 2016-01-04T13:00:00Z | m | 10 | 52.467488 | 13.402115 | 48 | certain | 4.5 | m/sec | high | 90 | degrees | high
Berlin-Tempelhof | 2016-01-04T14:00:00Z | m | 10 | 52.467488 | 13.402115 | 48 | certain | 4.6 | m/sec | high | 80 | degrees | high
Berlin-Tempelhof | 2016-01-04T15:00:00Z | m | 10 | 52.467488 | 13.402115 | 48 | certain | 5.3 | m/sec | high | 90 | degrees | high
Berlin-Tempelhof | 2016-01-04T16:00:00Z | m | 10 | 52.467488 | 13.402115 | 48 | certain | 5.1 | m/sec | high | 90 | degrees | high
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

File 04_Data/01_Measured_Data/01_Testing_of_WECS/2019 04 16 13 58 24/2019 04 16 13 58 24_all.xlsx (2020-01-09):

Year | Month | Day | Hour | Minute | Second | V1 | V2 | I1 | I2 | P1 | P2 | SU_MS | SU_Stability | MS | MS_RPM | Gen_RPM | SU_P_1_target | SU_Gen_Start_Counter | Relais_state | wind_v1 | wind_v1_mean | wind_v1_cut_out | wind_status | Battery_full | MS_DCDC_PWM | Dumpload | Short_Break | MPPT_MODE | MPPT_delta_wind_v1 | MPPT_delta_wind_v1_R | MPPT_DCDC_PWM | MPPT_omega_stern | MPPT_omega_opt | MPPT_kopt_e6 | MPPT_P_2_opt | MPPT_delta_P_2 | MPPT_delta_Omega | Codepoint | v1_new | RPM_Turb
2019 | 4 | 16 | 13 | 58 | 24 | 17.256 | 12.34 | Nan | -0.124 | Nan | -1.53 | 0 | 0 | 0 | 0 | 0 | 0 | 0 | 0 | 2 | 0 | 8 | 0 | 0 | 240 | 0 | 0 | 0 | 0 | 0 | 200 | 0 | 0 | 0 | 0 | 0 | 0 | 1 | Nan | Nan
2019 | 4 | 16 | 13 | 59 | 25 | 16.674 | 12.338 | Nan | -0.131 | Nan | -1.62 | 0 | 0 | 0 | 0 | 0 | 0 | 0 | 0 | 2 | 2 | 8 | 2 | 0 | 240 | 0 | 0 | 0 | 0 | 0 | 240 | 0 | 0 | 0 | 0 | 0 | 0 | 2 | 3.3 | 0
2019 | 4 | 16 | 13 | 59 | 26 | 13.07 | 12.319 | Nan | -0.098 | Nan | -1.21 | 0 | 0 | 0 | 46 | 0 | 0 | 0 | 1 | 2 | 2 | 8 | 2 | 0 | 240 | 0 | 0 | 0 | 0 | 0 | 240 | 0 | 0 | 0 | 0 | 0 | 0 | 3 | 3.25 | 0
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

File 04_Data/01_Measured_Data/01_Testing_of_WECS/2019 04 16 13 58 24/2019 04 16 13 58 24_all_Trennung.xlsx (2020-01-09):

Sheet: Tabelle1
Year | Month | Day | Hour | Minute | Second | V1 | V2 | I1 | I2 | P1 | P2 | SU_MS | SU_Stability | MS | MS_RPM | Gen_RPM | SU_P_1_target | SU_Gen_Start_Counter | Relais_state | wind_v1 | wind_v1_mean | wind_v1_cut_out | wind_status | Battery_full | MS_DCDC_PWM | Dumpload | Short_Break | MPPT_MODE | MPPT_delta_wind_v1 | MPPT_delta_wind_v1_R | MPPT_DCDC_PWM | MPPT_omega_stern | MPPT_omega_opt | MPPT_kopt_e6 | MPPT_P_2_opt | MPPT_delta_P_2 | MPPT_delta_Omega | Codepoint | v1_new | RPM_Turb
2019 | 4 | 16 | 13 | 58 | 24 | 17.256 | 12.34 | Nan | -0.124 | Nan | -1.53 | 0 | 0 | 0 | 0 | 0 | 0 | 0 | 0 | 2 | 0 | 8 | 0 | 0 | 240 | 0 | 0 | 0 | 0 | 0 | 200 | 0 | 0 | 0 | 0 | 0 | 0 | 1 | Nan | Nan
2019 | 4 | 16 | 13 | 58 | 25 | Nan | Nan | Nan | Nan | Nan | Nan | Nan | Nan | Nan | Nan | Nan | Nan | Nan | Nan | Nan | Nan | Nan | Nan | Nan | Nan | Nan | Nan | Nan | Nan | Nan | Nan | Nan | Nan | Nan | Nan | Nan | Nan | Nan | Nan | Nan
2019 | 4 | 16 | 13 | 58 | 26 | Nan | Nan | Nan | Nan | Nan | Nan | Nan | Nan | Nan | Nan | Nan | Nan | Nan | Nan | Nan | Nan | Nan | Nan | Nan | Nan | Nan | Nan | Nan | Nan | Nan | Nan | Nan | Nan | Nan | Nan | Nan | Nan | Nan | Nan | Nan
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

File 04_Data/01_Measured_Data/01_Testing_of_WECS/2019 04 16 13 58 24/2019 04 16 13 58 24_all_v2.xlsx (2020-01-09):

Year | Month | Day | Hour | Minute | Second | V1 | V2 | I1 | I2 | P1 | P2 | SU_MS | SU_Stability | MS | MS_RPM | Gen_RPM | SU_P_1_target | SU_Gen_Start_Counter | Relais_state | wind_v1 | wind_v1_mean | wind_v1_cut_out | wind_status | Battery_full | MS_DCDC_PWM | Dumpload | Short_Break | MPPT_MODE | MPPT_delta_wind_v1 | MPPT_delta_wind_v1_R | MPPT_DCDC_PWM | MPPT_omega_stern | MPPT_omega_opt | MPPT_kopt_e6 | MPPT_P_2_opt | MPPT_delta_P_2 | MPPT_delta_Omega | Codepoint | v1_new | RPM_Turb
2019 | 4 | 16 | 13 | 58 | 24 | 17.256 | 12.34 | Nan | -0.124 | Nan | -1.53 | 0 | 0 | 0 | 0 | 0 | 0 | 0 | 0 | 2 | 0 | 8 | 0 | 0 | 240 | 0 | 0 | 0 | 0 | 0 | 200 | 0 | 0 | 0 | 0 | 0 | 0 | 1 | Nan | Nan
2019 | 4 | 16 | 13 | 58 | 27 | Nan | Nan | Nan | Nan | Nan | Nan | Nan | Nan | Nan | Nan | Nan | Nan | Nan | Nan | Nan | Nan | Nan | Nan | Nan | Nan | Nan | Nan | Nan | Nan | Nan | Nan | Nan | Nan | Nan | Nan | Nan | Nan | Nan | Nan | Nan
2019 | 4 | 16 | 13 | 58 | 30 | Nan | Nan | Nan | Nan | Nan | Nan | Nan | Nan | Nan | Nan | Nan | Nan | Nan | Nan | Nan | Nan | Nan | Nan | Nan | Nan | Nan | Nan | Nan | Nan | Nan | Nan | Nan | Nan | Nan | Nan | Nan | Nan | Nan | Nan | Nan
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

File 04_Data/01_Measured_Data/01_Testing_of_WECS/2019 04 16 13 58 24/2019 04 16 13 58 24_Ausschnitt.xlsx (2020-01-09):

Year | Month | Day | Hour | Minute | Second | V1 | V2 | I2 | P2 | SU_MS | MS_RPM | Gen_RPM | SU_P_1_target | SU_Gen_Start_Counter | Relais_state | MS_DCDC_PWM | MPPT_MODE | MPPT_DCDC_PWM | RPM_Turb
2019 | 4 | 16 | 14 | 24 | 25 | 27.552 | 11.818 | -1.866 | -22.05 | 153 | 100 | 0 | -23.57 | 0 | 1 | 105 | 0 | 240 | 86.58
2019 | 4 | 16 | 14 | 24 | 27 | 27.532 | 11.813 | -1.911 | -22.57 | 153 | 100 | 0 | -23.57 | 0 | 1 | 105 | 0 | 240 | 87
2019 | 4 | 16 | 14 | 24 | 28 | 27.563 | 11.817 | -1.878 | -22.19 | 153 | 100 | 0 | -23.57 | 0 | 1 | 105 | 0 | 240 | 87.21
2019 | 4 | 16 | 14 | 24 | 30 | 29.455 | 12.157 | -0.162 | -1.97 | 153 | 74 | 78 | -23.57 | 0 | 0 | 105 | 0 | 105 | 86.3
2019 | 4 | 16 | 14 | 24 | 31 | 29.476 | 12.165 | -0.164 | -2 | 0 | 12 | 73 | -23.57 | 0 | 0 | 105 | 0 | 105 | 85.84
2019 | 4 | 16 | 14 | 24 | 32 | 28.153 | 12.172 | -0.164 | -2 | 0 | 0 | 66 | -23.57 | 0 | 0 | 110 | 3 | 110 | 80.29
2019 | 4 | 16 | 14 | 24 | 33 | 26.944 | 12.178 | -0.159 | -1.93 | 0 | 0 | 60 | -23.57 | 0 | 0 | 115 | 3 | 115 | 74.75
2019 | 4 | 16 | 14 | 24 | 34 | 25.831 | 12.182 | -0.159 | -1.94 | 0 | 0 | 55 | -23.57 | 0 | 0 | 120 | 3 | 120 | 69.2
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

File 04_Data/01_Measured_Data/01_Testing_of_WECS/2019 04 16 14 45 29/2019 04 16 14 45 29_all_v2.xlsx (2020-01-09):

Year | Month | Day | Hour | Minute | Second | V1 | V2 | I1 | I2 | P1 | P2 | SU_MS | SU_Stability | MS | MS_RPM | Gen_RPM | SU_P_1_target | SU_Gen_Start_Counter | Relais_state | wind_v1 | wind_v1_mean | wind_v1_cut_out | wind_status | Battery_full | MS_DCDC_PWM | Dumpload | Short_Break | MPPT_MODE | MPPT_delta_wind_v1 | MPPT_delta_wind_v1_R | MPPT_DCDC_PWM | MPPT_omega_stern | MPPT_omega_opt | MPPT_kopt_e6 | MPPT_P_2_opt | MPPT_delta_P_2 | MPPT_delta_Omega | Codepoint | v1_new | RPM_Turb
2019 | 4 | 16 | 14 | 45 | 29 | 24.262 | 12.266 | Nan | -0.133 | Nan | -1.63 | 0 | 0 | 0 | 0 | 0 | 0 | 0 | 0 | 2 | 0 | 8 | 0 | 0 | 240 | 0 | 0 | 0 | 0 | 0 | 200 | 0 | 0 | 0 | 0 | 0 | 0 | 1 | Nan | Nan
2019 | 4 | 16 | 14 | 45 | 32 | Nan | Nan | Nan | Nan | Nan | Nan | Nan | Nan | Nan | Nan | Nan | Nan | Nan | Nan | Nan | Nan | Nan | Nan | Nan | Nan | Nan | Nan | Nan | Nan | Nan | Nan | Nan | Nan | Nan | Nan | Nan | Nan | Nan | Nan | Nan
2019 | 4 | 16 | 14 | 45 | 35 | Nan | Nan | Nan | Nan | Nan | Nan | Nan | Nan | Nan | Nan | Nan | Nan | Nan | Nan | Nan | Nan | Nan | Nan | Nan | Nan | Nan | Nan | Nan | Nan | Nan | Nan | Nan | Nan | Nan | Nan | Nan | Nan | Nan | Nan | Nan
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

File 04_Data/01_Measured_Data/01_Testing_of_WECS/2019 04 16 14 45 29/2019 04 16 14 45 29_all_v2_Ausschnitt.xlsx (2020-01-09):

Year | Month | Day | Hour | Minute | Second | V1 | V2 | I2 | P2 | SU_MS | MS_RPM | Gen_RPM | SU_P_1_target | Relais_state | MS_DCDC_PWM | MPPT_MODE | MPPT_DCDC_PWM | v1_new | RPM_Turb
2019 | 4 | 16 | 14 | 59 | 46 | 27.568 | 11.818 | -1.909 | -22.56 | 154 | 100 | 0 | -23.96 | 1 | 105 | 0 | 240 | 8.17 | 81.04
2019 | 4 | 16 | 14 | 59 | 49 | Nan | Nan | Nan | Nan | Nan | Nan | Nan | Nan | Nan | Nan | Nan | Nan | 7.07 | 80.97
2019 | 4 | 16 | 14 | 59 | 52 | Nan | Nan | Nan | Nan | Nan | Nan | Nan | Nan | Nan | Nan | Nan | Nan | 6.5 | 81.19
2019 | 4 | 16 | 14 | 59 | 55 | Nan | Nan | Nan | Nan | Nan | Nan | Nan | Nan | Nan | Nan | Nan | Nan | 5.97 | 81.37
2019 | 4 | 16 | 14 | 59 | 58 | Nan | Nan | Nan | Nan | Nan | Nan | Nan | Nan | Nan | Nan | Nan | Nan | 7.02 | 81.63
2019 | 4 | 16 | 15 | 0 | 1 | Nan | Nan | Nan | Nan | Nan | Nan | Nan | Nan | Nan | Nan | Nan | Nan | 6.55 | 81.89
2019 | 4 | 16 | 15 | 0 | 4 | Nan | Nan | Nan | Nan | Nan | Nan | Nan | Nan | Nan | Nan | Nan | Nan | 6.08 | 81.97
2019 | 4 | 16 | 15 | 0 | 7 | Nan | Nan | Nan | Nan | Nan | Nan | Nan | Nan | Nan | Nan | Nan | Nan | 6.86 | 82.04
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

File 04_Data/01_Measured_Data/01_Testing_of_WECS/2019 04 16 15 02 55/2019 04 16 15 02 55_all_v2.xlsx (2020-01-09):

Year | Month | Day | Hour | Minute | Second | V1 | V2 | I1 | I2 | P1 | P2 | SU_MS | SU_Stability | MS | MS_RPM | Gen_RPM | SU_P_1_target | SU_Gen_Start_Counter | Relais_state | wind_v1 | wind_v1_mean | wind_v1_cut_out | wind_status | Battery_full | MS_DCDC_PWM | Dumpload | Short_Break | MPPT_MODE | MPPT_delta_wind_v1 | MPPT_delta_wind_v1_R | MPPT_DCDC_PWM | MPPT_omega_stern | MPPT_omega_opt | MPPT_kopt_e6 | MPPT_P_2_opt | MPPT_delta_P_2 | MPPT_delta_Omega | Codepoint | v1_new | RPM_Turb
2019 | 4 | 16 | 15 | 2 | 55 | 26.695 | 12.234 | Nan | -0.135 | Nan | -1.65 | 0 | 0 | 0 | 0 | 0 | 0 | 0 | 0 | 2 | 0 | 8 | 0 | 0 | 240 | 0 | 0 | 0 | 0 | 0 | 200 | 0 | 0 | 0 | 0 | 0 | 0 | 1 | Nan | Nan
2019 | 4 | 16 | 15 | 2 | 58 | Nan | Nan | Nan | Nan | Nan | Nan | Nan | Nan | Nan | Nan | Nan | Nan | Nan | Nan | Nan | Nan | Nan | Nan | Nan | Nan | Nan | Nan | Nan | Nan | Nan | Nan | Nan | Nan | Nan | Nan | Nan | Nan | Nan | Nan | Nan
2019 | 4 | 16 | 15 | 3 | 1 | Nan | Nan | Nan | Nan | Nan | Nan | Nan | Nan | Nan | Nan | Nan | Nan | Nan | Nan | Nan | Nan | Nan | Nan | Nan | Nan | Nan | Nan | Nan | Nan | Nan | Nan | Nan | Nan | Nan | Nan | Nan | Nan | Nan | Nan | Nan
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

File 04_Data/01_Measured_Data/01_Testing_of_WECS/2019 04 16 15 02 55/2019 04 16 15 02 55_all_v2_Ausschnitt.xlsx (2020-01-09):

Year | Month | Day | Hour | Minute | Second | V1 | V2 | I2 | P2 | SU_MS | MS_RPM | Gen_RPM | Relais_state | MS_DCDC_PWM | MPPT_MODE | MPPT_DCDC_PWM | v1_new | RPM_Turb
2019 | 4 | 16 | 15 | 17 | 39 | 27.749 | 11.785 | -1.938 | -22.84 | 152 | 100 | 0 | 1 | 104 | 0 | 240 | 4.03 | 81.85
2019 | 4 | 16 | 15 | 17 | 40 | 27.734 | 11.783 | -1.902 | -22.41 | 152 | 100 | 0 | 1 | 104 | 0 | 240 | 3.82 | 82.08
2019 | 4 | 16 | 15 | 17 | 43 | Nan | Nan | Nan | Nan | Nan | Nan | Nan | Nan | Nan | Nan | Nan | 4.35 | 82.45
2019 | 4 | 16 | 15 | 17 | 46 | Nan | Nan | Nan | Nan | Nan | Nan | Nan | Nan | Nan | Nan | Nan | 4.19 | 82.6
2019 | 4 | 16 | 15 | 17 | 49 | Nan | Nan | Nan | Nan | Nan | Nan | Nan | Nan | Nan | Nan | Nan | 4.45 | 82.95
2019 | 4 | 16 | 15 | 17 | 52 | Nan | Nan | Nan | Nan | Nan | Nan | Nan | Nan | Nan | Nan | Nan | 4.82 | 83.25
2019 | 4 | 16 | 15 | 17 | 55 | Nan | Nan | Nan | Nan | Nan | Nan | Nan | Nan | Nan | Nan | Nan | 4.66 | 83.49
2019 | 4 | 16 | 15 | 17 | 58 | Nan | Nan | Nan | Nan | Nan | Nan | Nan | Nan | Nan | Nan | Nan | 5.6 | 83.88
2019 | 4 | 16 | 15 | 18 | 1 | Nan | Nan | Nan | Nan | Nan | Nan | Nan | Nan | Nan | Nan | Nan | 5.81 | 84.35
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

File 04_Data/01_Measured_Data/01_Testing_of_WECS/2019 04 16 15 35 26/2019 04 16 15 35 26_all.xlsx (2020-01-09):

Year | Month | Day | Hour | Minute | Second | V1 | V2 | I1 | I2 | P1 | P2 | SU_MS | SU_Stability | MS | MS_RPM | Gen_RPM | SU_P_1_target | SU_Gen_Start_Counter | Relais_state | wind_v1 | wind_v1_mean | wind_v1_cut_out | wind_status | Battery_full | MS_DCDC_PWM | Dumpload | Short_Break | MPPT_MODE | MPPT_delta_wind_v1 | MPPT_delta_wind_v1_R | MPPT_DCDC_PWM | MPPT_omega_stern | MPPT_omega_opt | MPPT_kopt_e6 | MPPT_P_2_opt | MPPT_delta_P_2 | MPPT_delta_Omega | Codepoint | v1_new | RPM_Turb
2019 | 4 | 16 | 15 | 35 | 26 | 16.386 | 12.267 | Nan | -0.112 | Nan | -1.38 | 0 | 0 | 0 | 0 | 0 | 0 | 0 | 0 | 2 | 0 | 8 | 0 | 0 | 240 | 0 | 0 | 0 | 0 | 0 | 200 | 0 | 0 | 0 | 0 | 0 | 0 | 1 | 4.24 | 0
2019 | 4 | 16 | 15 | 35 | 29 | Nan | Nan | Nan | Nan | Nan | Nan | Nan | Nan | Nan | Nan | Nan | Nan | Nan | Nan | Nan | Nan | Nan | Nan | Nan | Nan | Nan | Nan | Nan | Nan | Nan | Nan | Nan | Nan | Nan | Nan | Nan | Nan | Nan | 4.56 | 0
2019 | 4 | 16 | 15 | 35 | 32 | Nan | Nan | Nan | Nan | Nan | Nan | Nan | Nan | Nan | Nan | Nan | Nan | Nan | Nan | Nan | Nan | Nan | Nan | Nan | Nan | Nan | Nan | Nan | Nan | Nan | Nan | Nan | Nan | Nan | Nan | Nan | Nan | Nan | 4.24 | 0
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

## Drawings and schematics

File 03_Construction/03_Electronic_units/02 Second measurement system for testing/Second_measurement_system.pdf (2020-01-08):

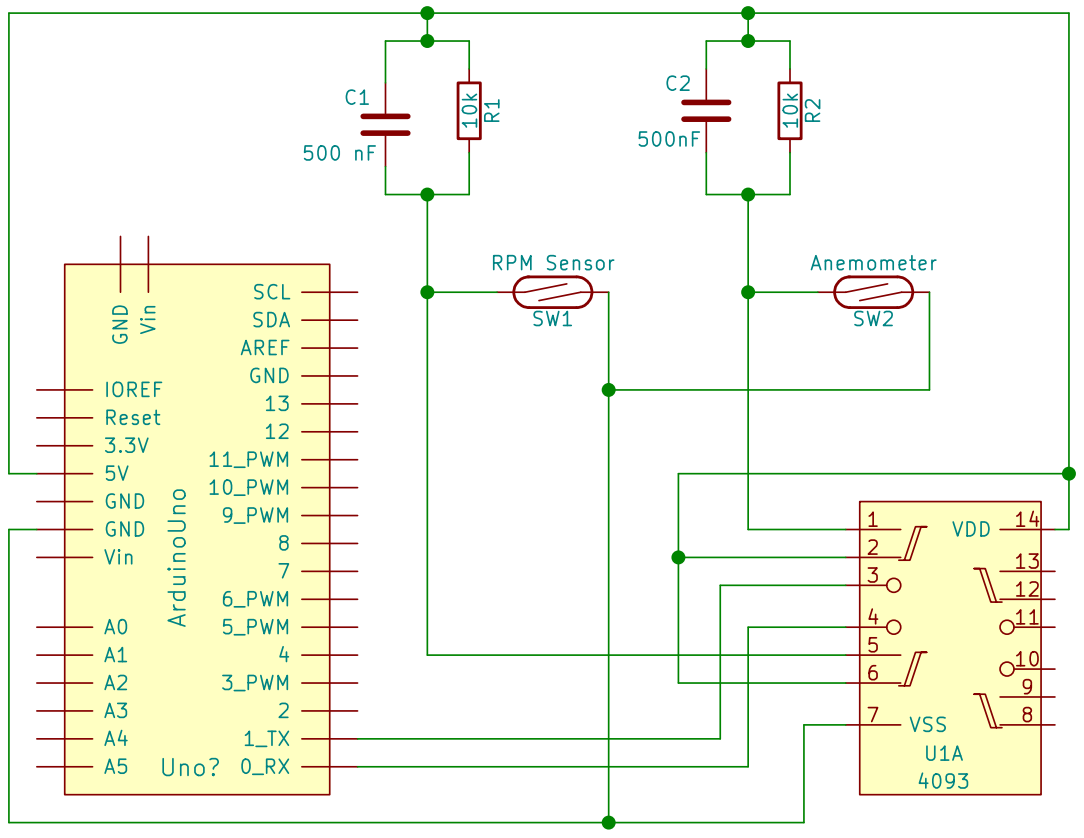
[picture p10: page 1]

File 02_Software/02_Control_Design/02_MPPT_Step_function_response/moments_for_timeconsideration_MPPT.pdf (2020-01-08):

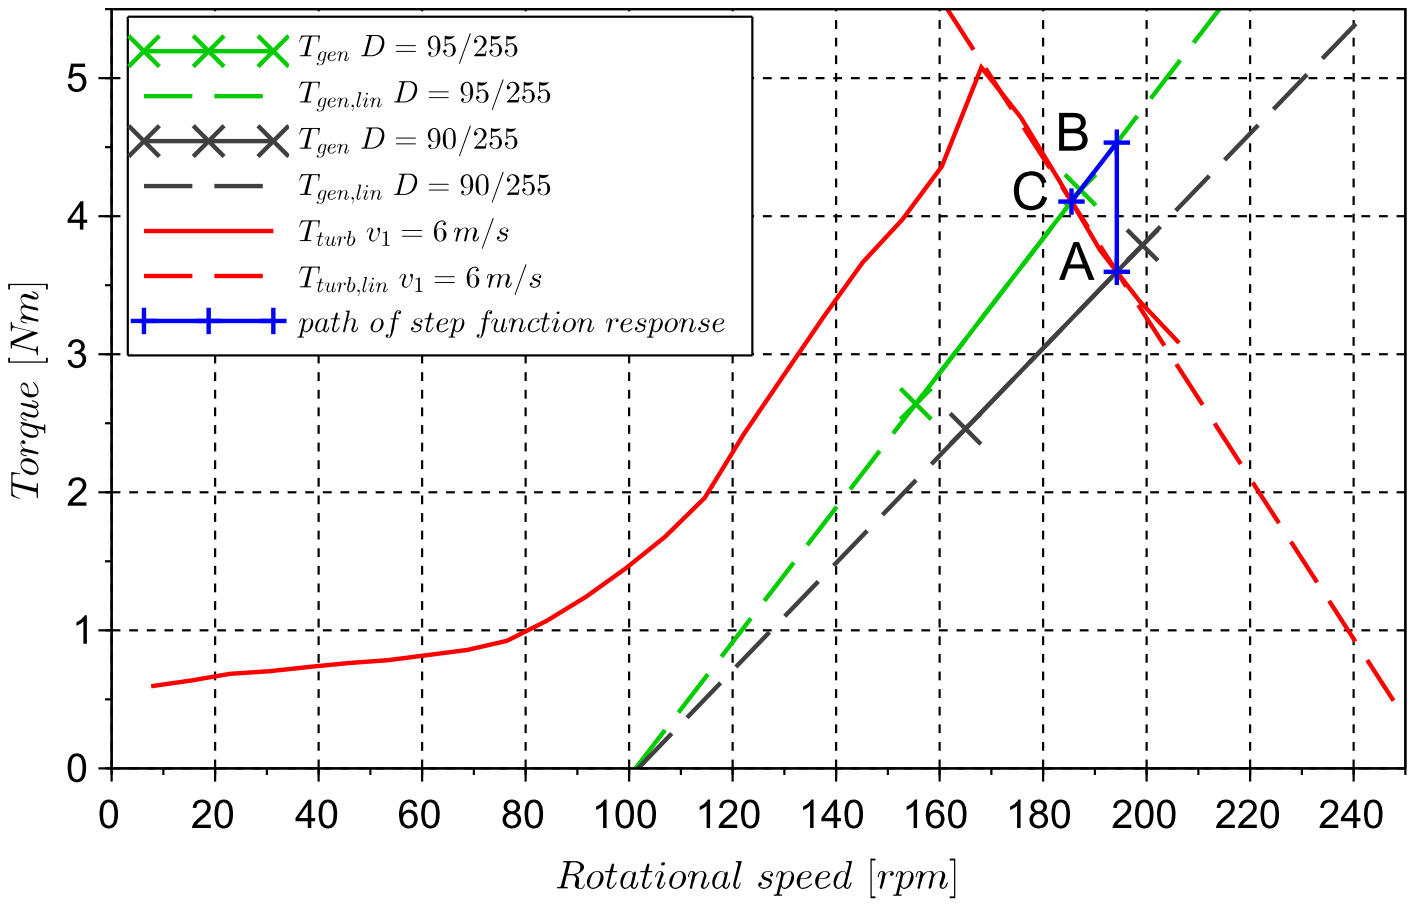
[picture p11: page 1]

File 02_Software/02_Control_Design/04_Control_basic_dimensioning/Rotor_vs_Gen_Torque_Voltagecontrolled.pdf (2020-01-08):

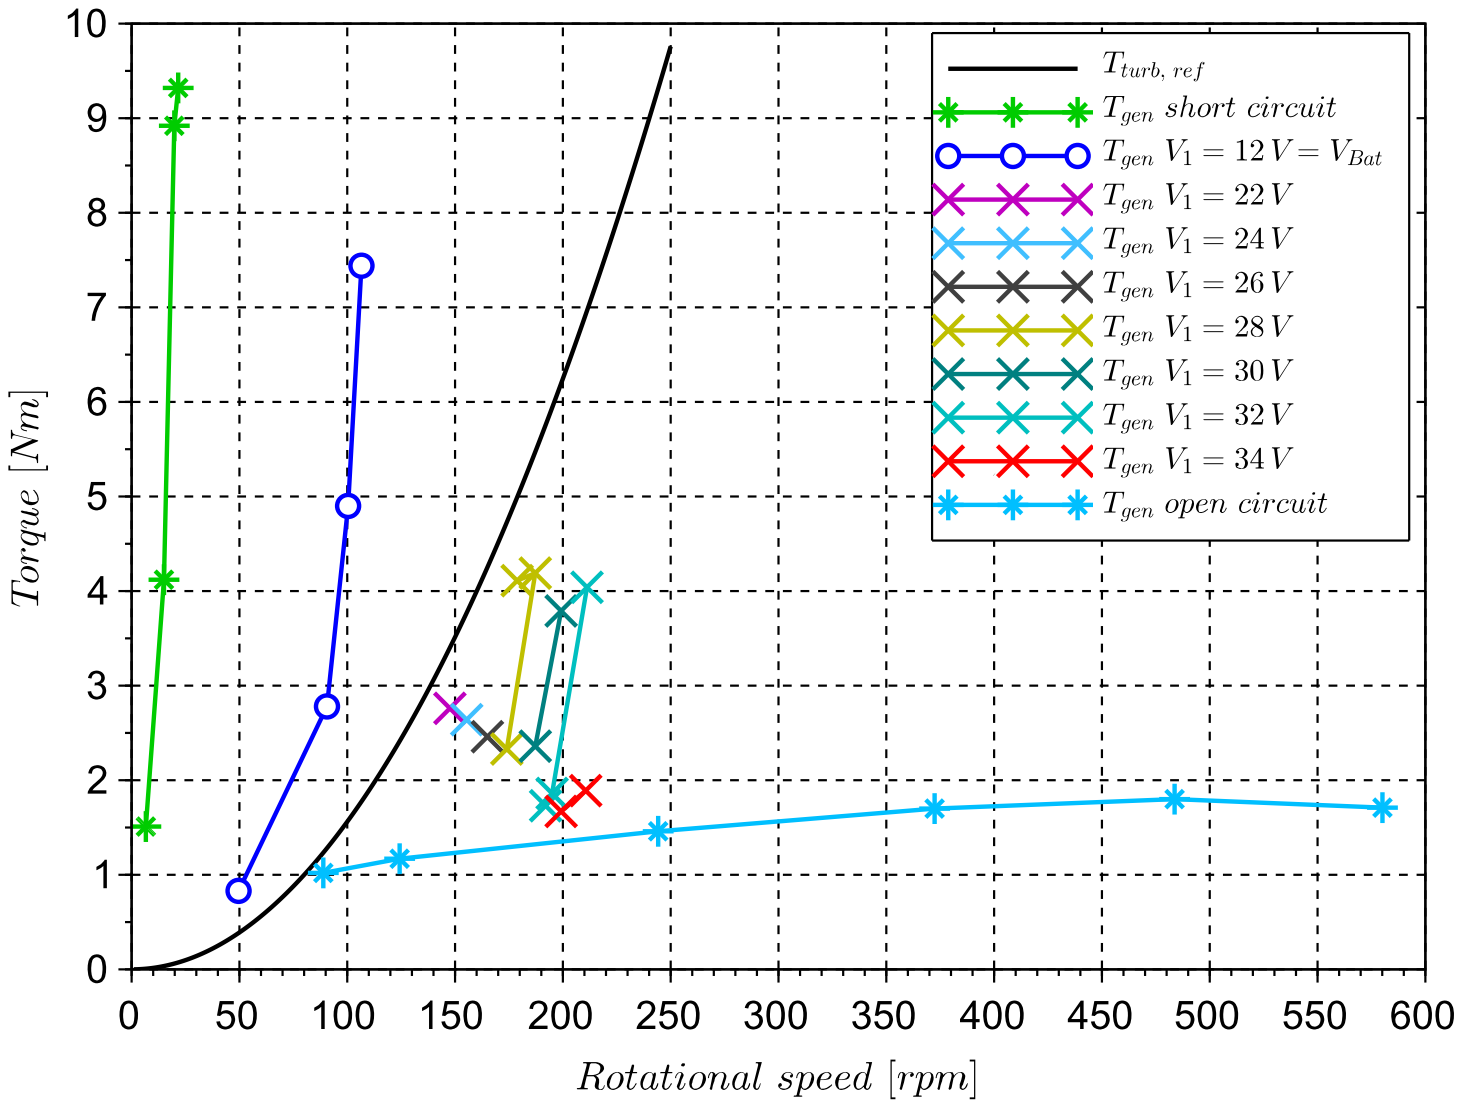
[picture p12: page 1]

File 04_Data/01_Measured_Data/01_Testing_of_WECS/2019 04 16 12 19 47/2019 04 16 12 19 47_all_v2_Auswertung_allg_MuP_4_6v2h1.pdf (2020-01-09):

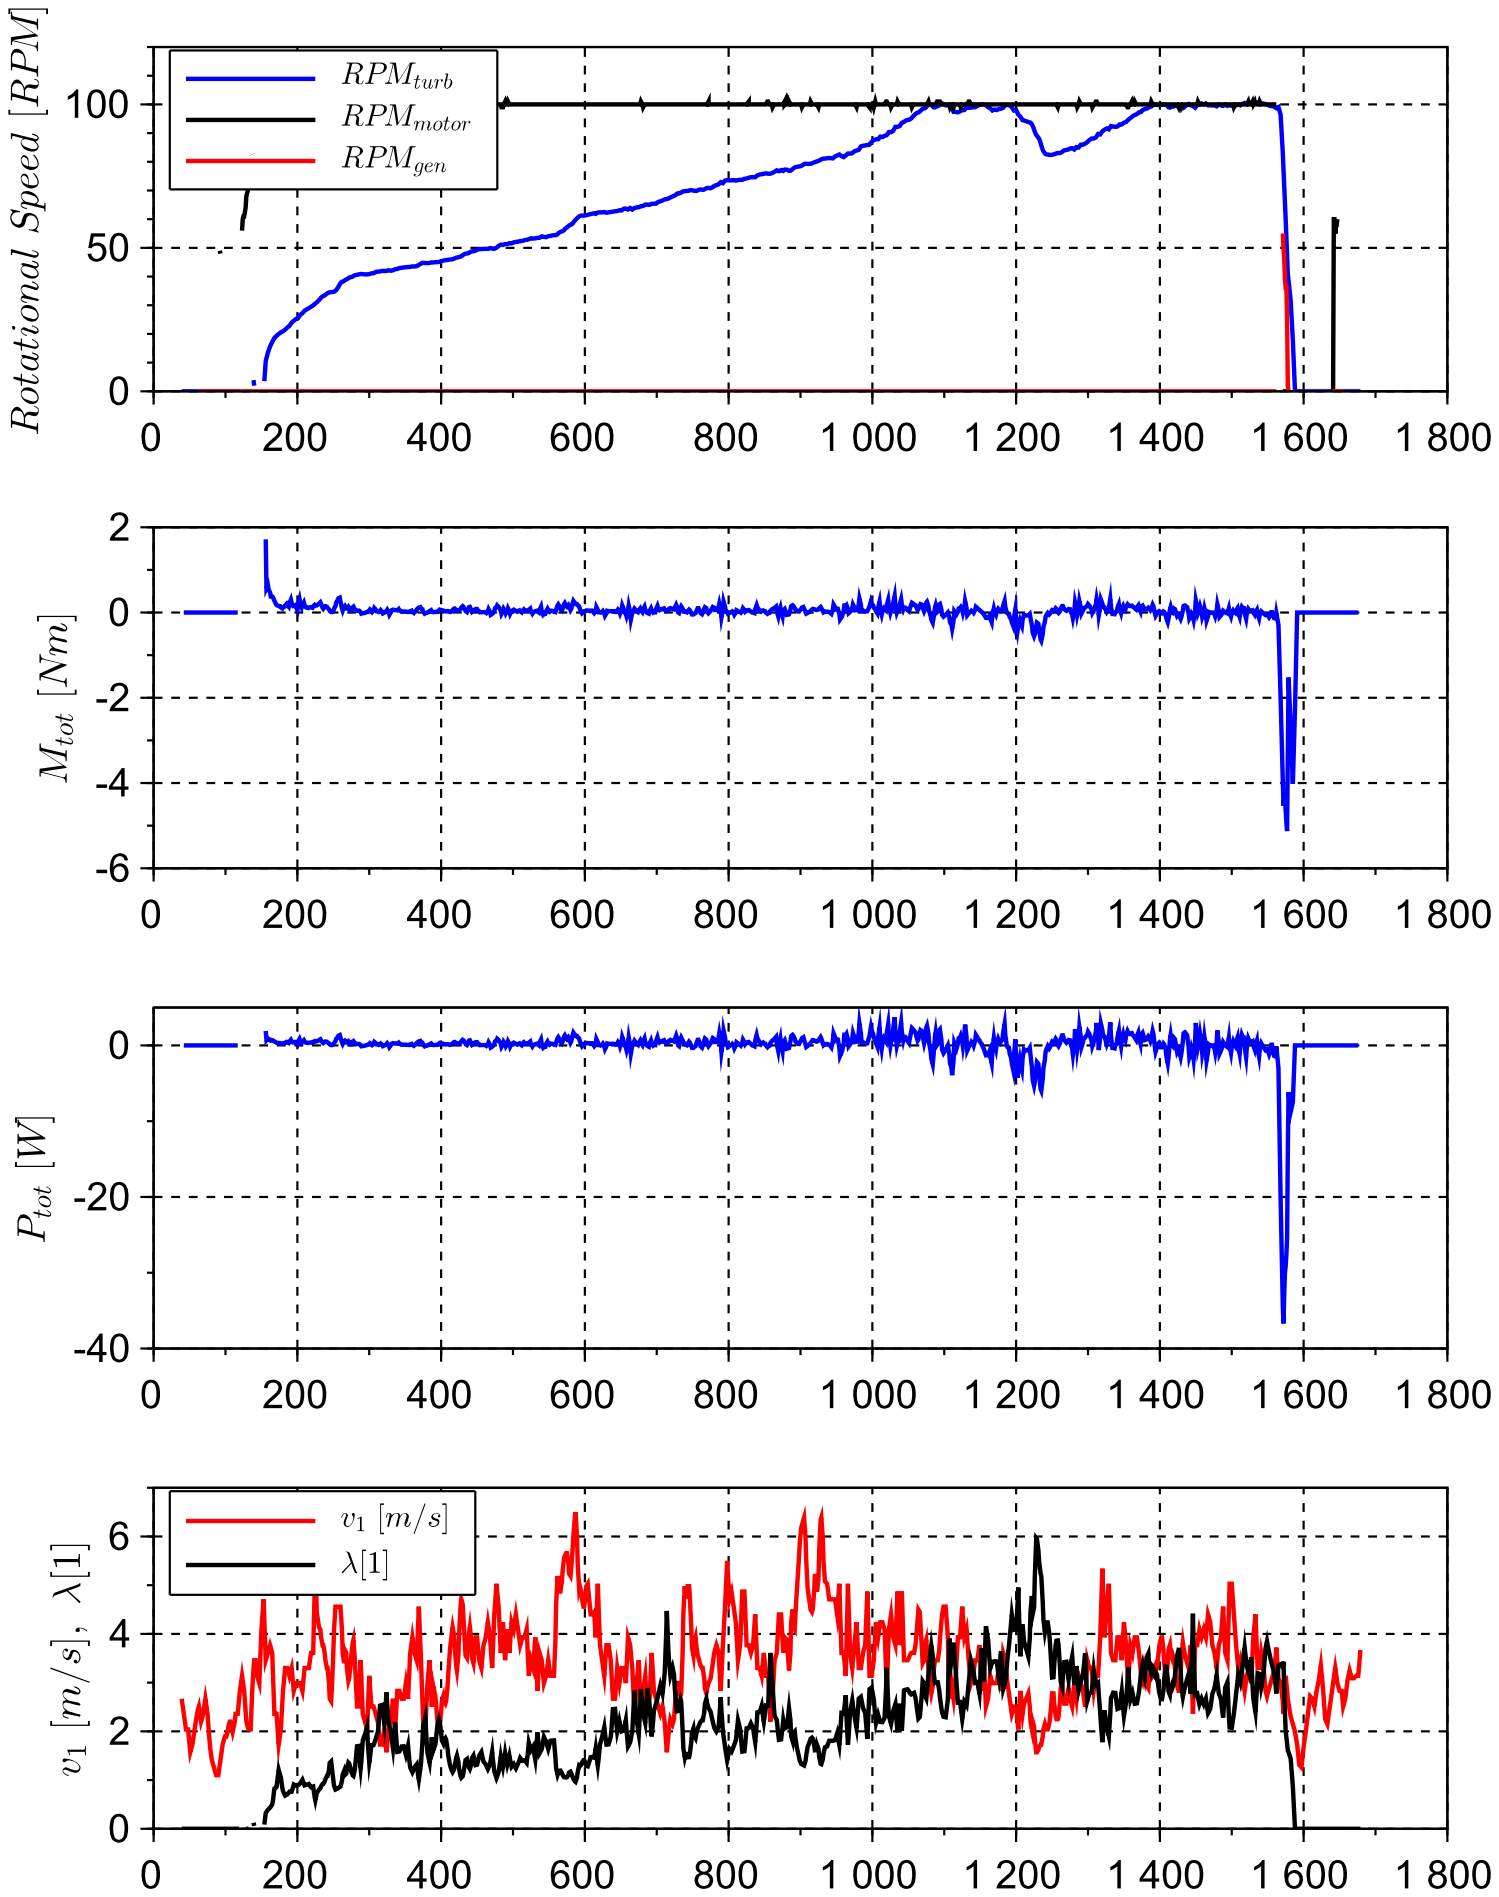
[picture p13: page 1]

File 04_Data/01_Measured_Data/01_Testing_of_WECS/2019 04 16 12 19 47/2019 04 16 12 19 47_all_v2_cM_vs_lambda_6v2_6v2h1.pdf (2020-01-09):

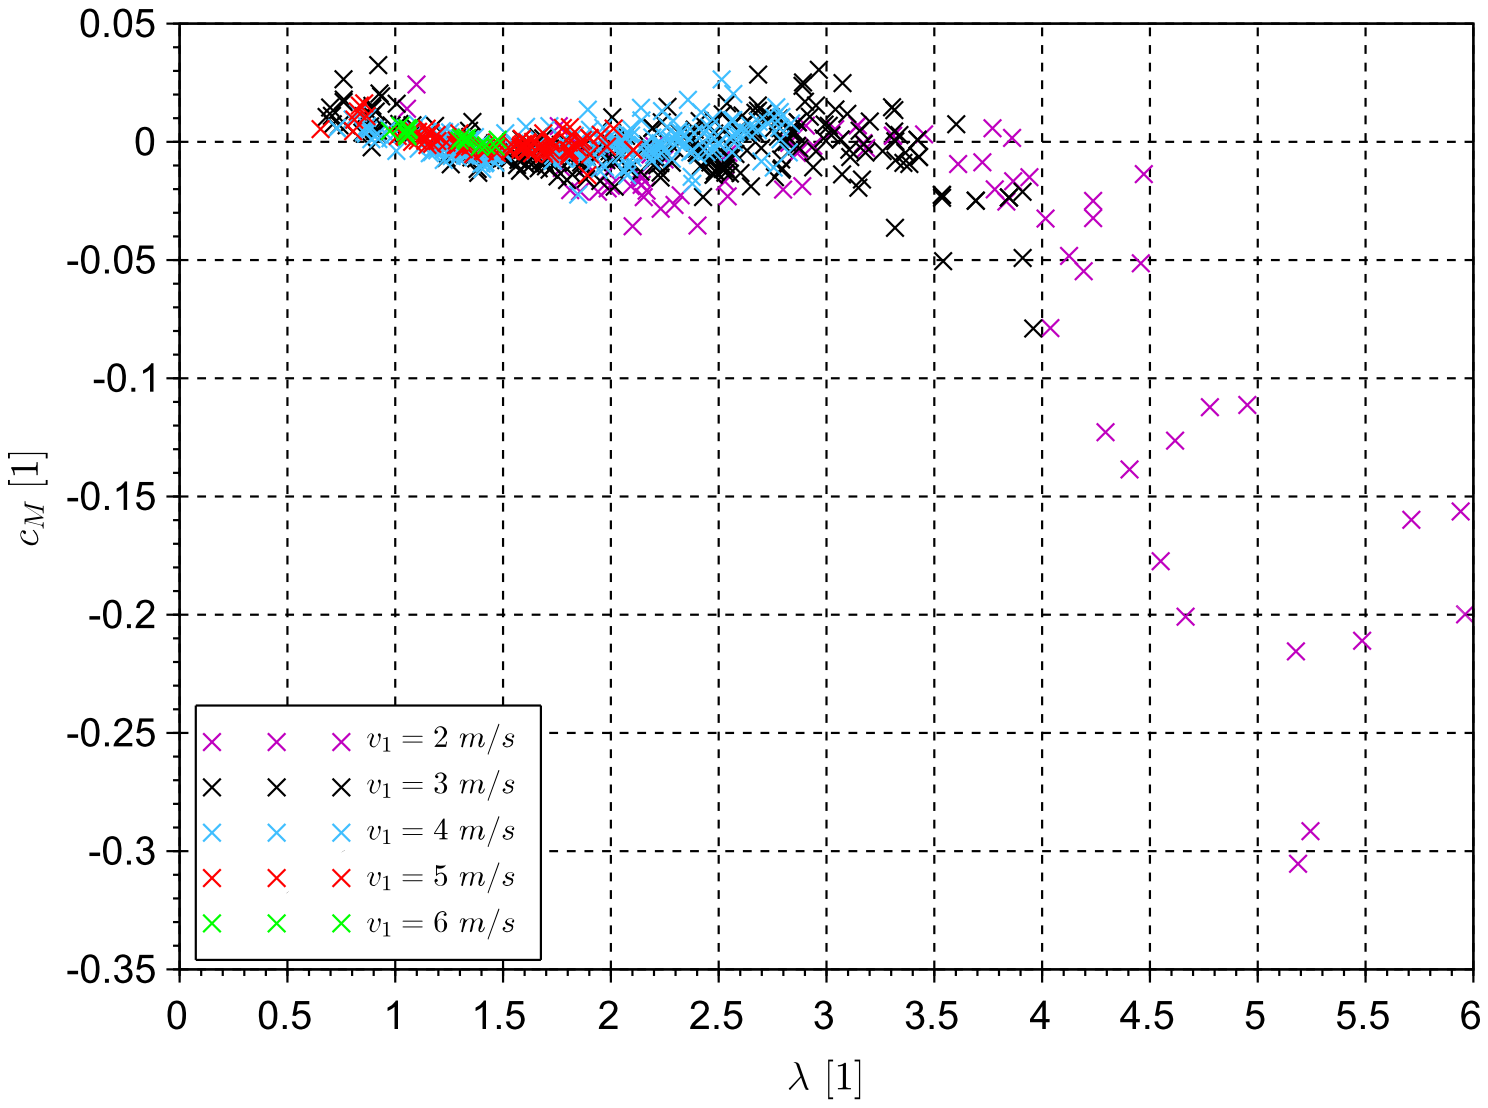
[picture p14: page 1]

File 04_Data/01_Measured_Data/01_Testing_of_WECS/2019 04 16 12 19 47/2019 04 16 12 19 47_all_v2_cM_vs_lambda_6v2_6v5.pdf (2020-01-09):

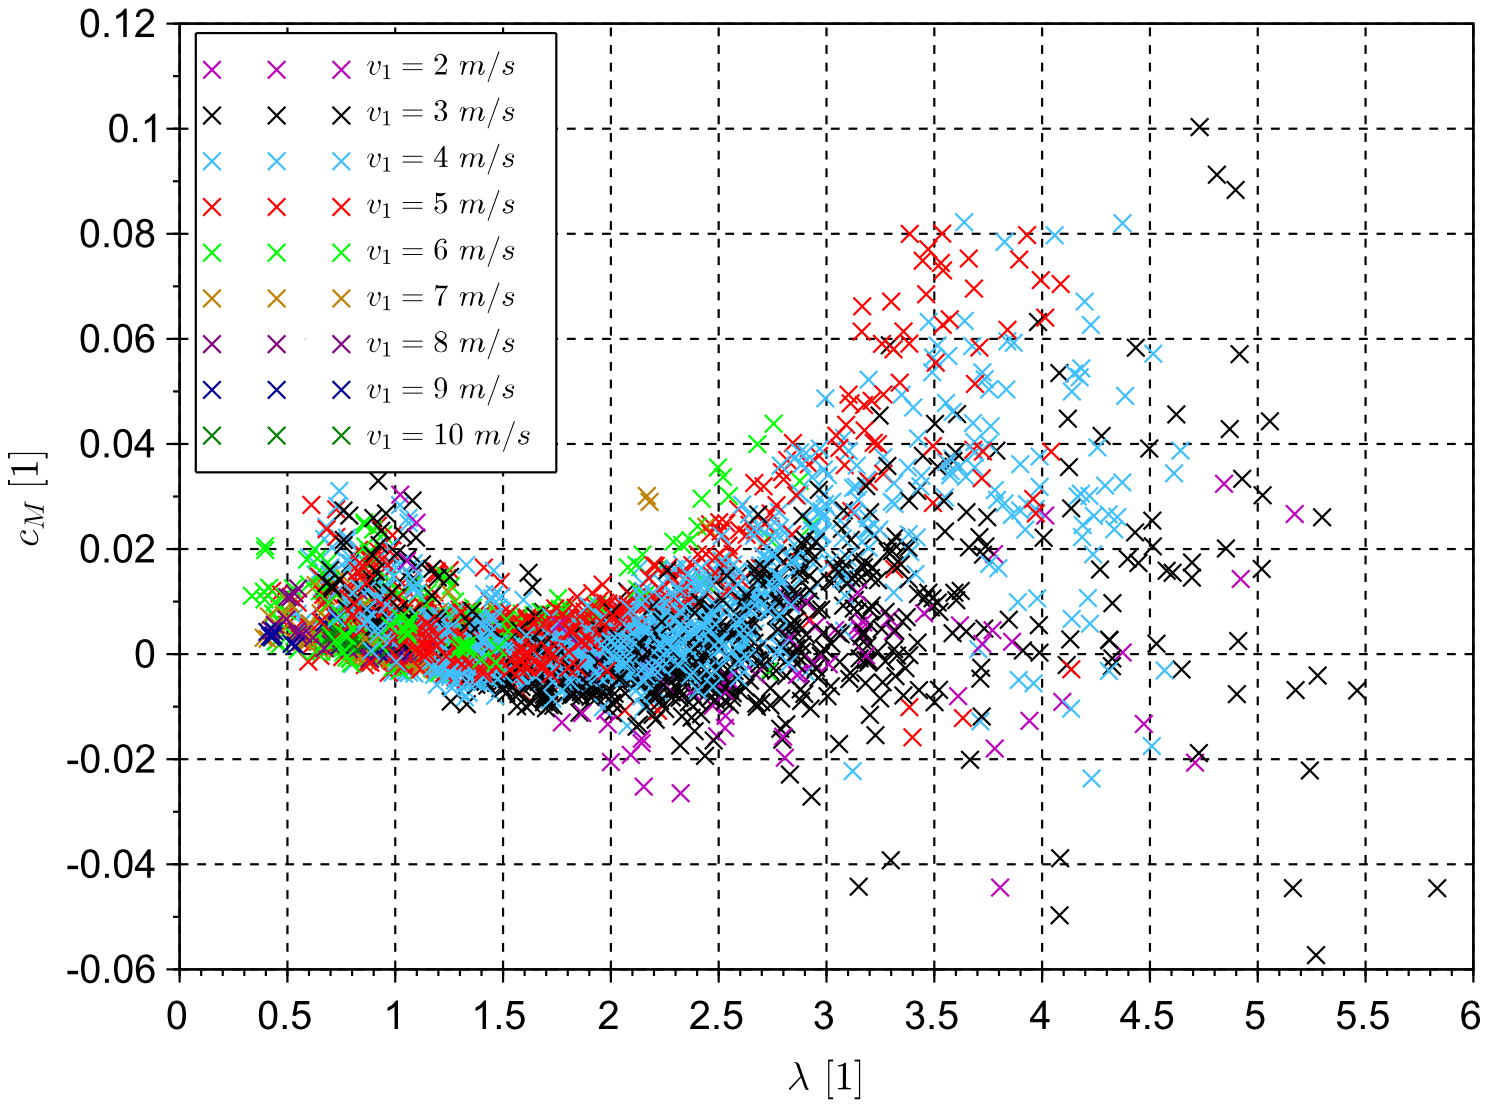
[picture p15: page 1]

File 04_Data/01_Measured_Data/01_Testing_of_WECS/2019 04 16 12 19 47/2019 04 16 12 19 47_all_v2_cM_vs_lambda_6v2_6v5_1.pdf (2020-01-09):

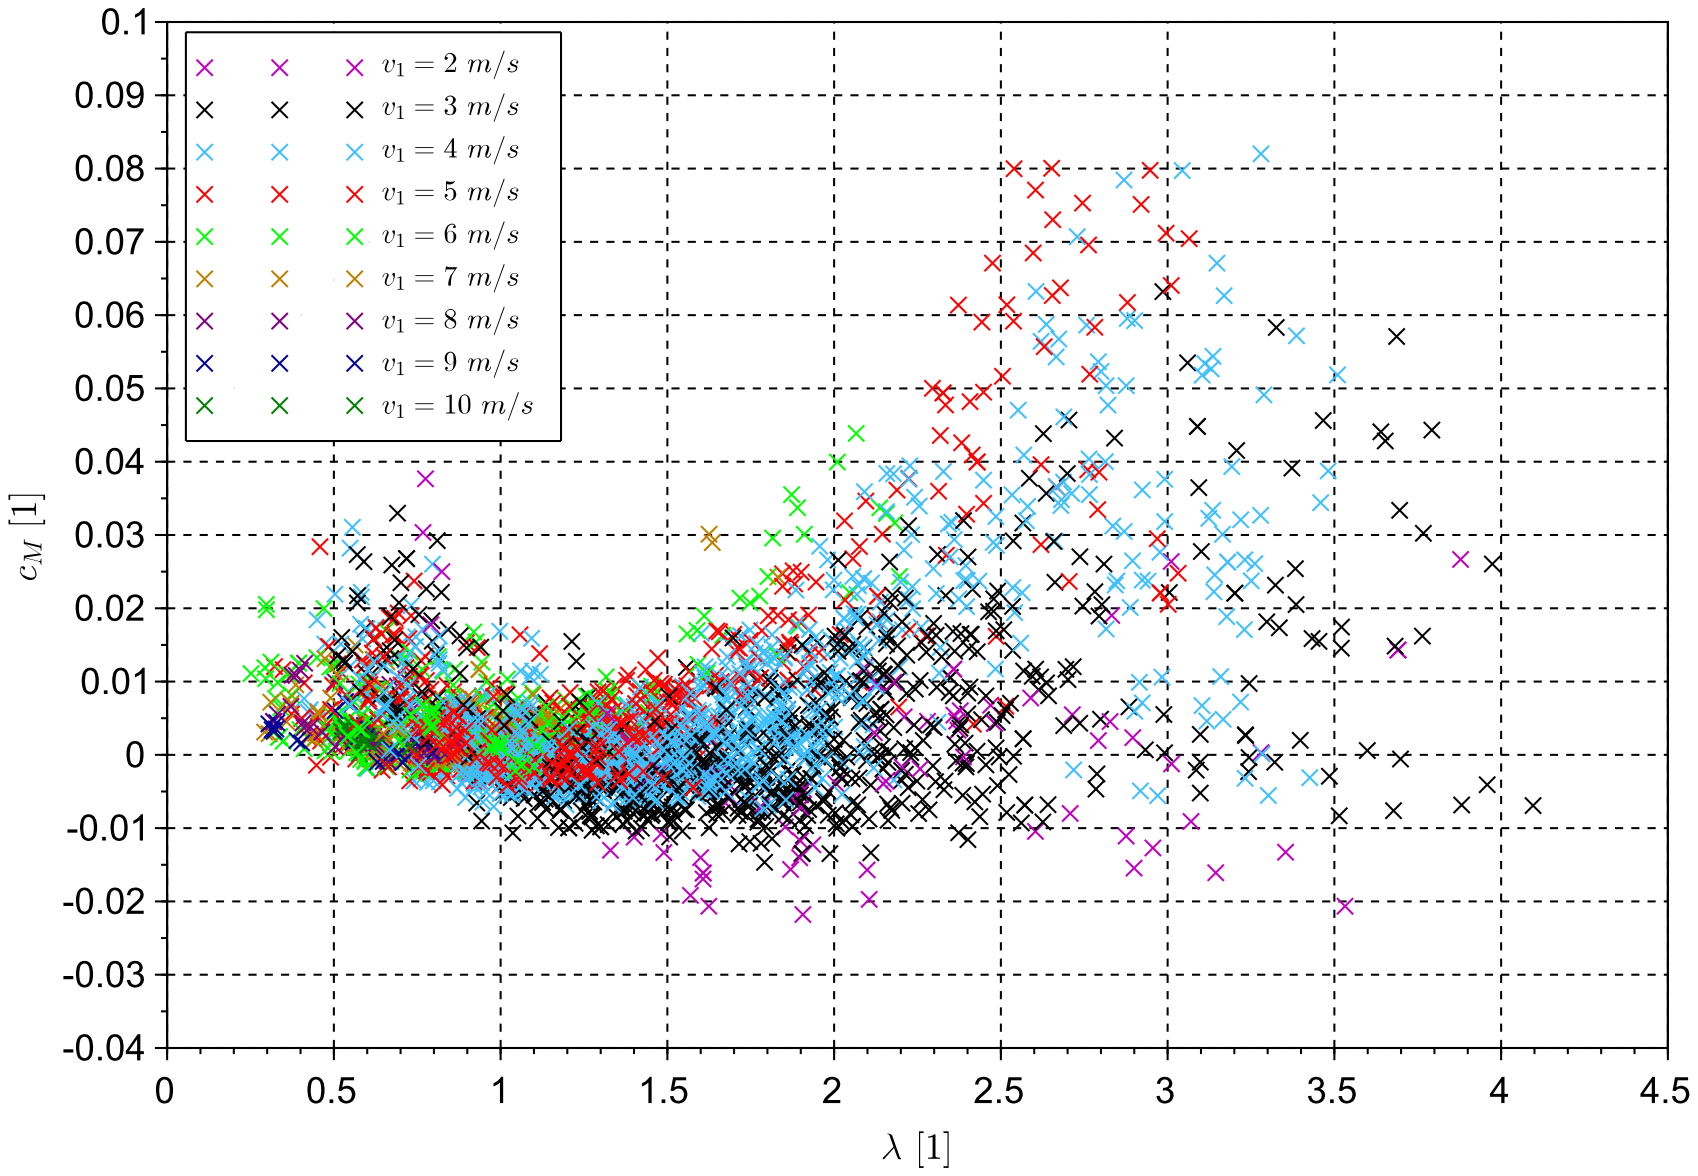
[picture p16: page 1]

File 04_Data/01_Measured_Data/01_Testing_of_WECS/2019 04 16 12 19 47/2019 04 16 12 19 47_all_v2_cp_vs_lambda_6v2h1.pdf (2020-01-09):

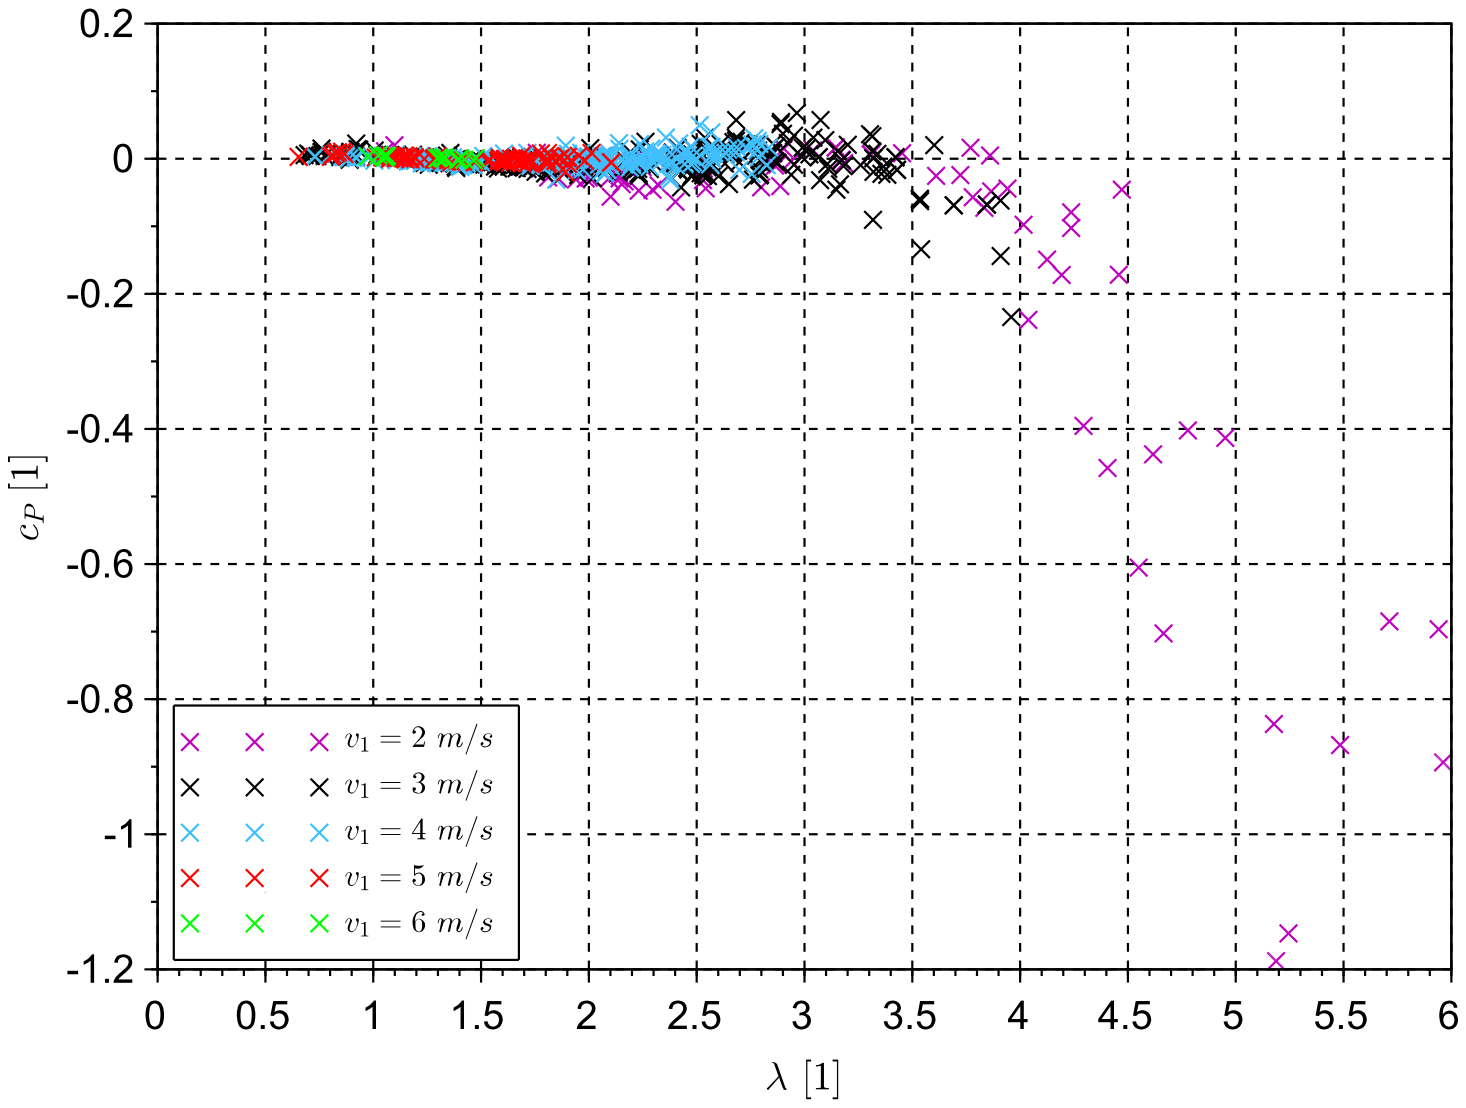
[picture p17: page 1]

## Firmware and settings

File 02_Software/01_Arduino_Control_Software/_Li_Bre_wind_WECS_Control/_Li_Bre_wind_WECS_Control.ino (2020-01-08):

//                       LiBre Wind: WECS Control   v 1.0                       //
//                             Overall controll                                 //
// This software is designed to be used with the Circuit Board B1v8 to controll //
//                a Stand Alone Wind Energy Conversion System                   //

//  Copyright (C) 2019  Julian Brendel julian.brendel@gmx.de under GNU GPLv3    //
//
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

////Include Libraries
#include <LiquidCrystal_I2C.h>
#include <Wire.h>
#include <Adafruit_ADS1015.h>
#include <DS3231.h>
#include <SPI.h>
#include <SD.h>

//// PINS ////
const int MS_RPM_interrupt_PIN=2;
const int Gen_PWM_interrupt_PIN = 3;
const int MS_outputPin = 4;
const int Relais_FET_PIN=5;
const int MS_Sensor_pulsewidth_PIN=7;
const int Dumpload_FET=8;
const int Short_Break_FET=9;
const int DCDC_Treiber_SD_Quer=10;
const int DCDC_PWM_PIN = 11;
const int wind_interrupt_PIN = 18;
const int Sec_interrupt_PIN=19;
const int Status_LED_red=22;
const int Status_LED_yellow=23;
const int Status_LED_blue=24;
const int Status_LED_green=25;
const int SU_LED_Pin=6;
const int SD_Card_CS = 53;

////Initialise RTC////
#define DS3231_ADDRESSE 0x68
DS3231 clock;
RTCDateTime dt;
int Sec=0;

////Initialise LCD////
LiquidCrystal_I2C lcd(0x27, 2, 1, 0, 4, 5, 6, 7, 3, POSITIVE);  // Set the LCD I2C address// PINS /////////////

//////Variable Declaraion//////
////Batterie check////
int Battery_full=0;                   // Batterie status
const float Battery_V2_High=14;       // Set Voltage when Batterie is full
const float Battery_V2_Low=12.5;      // Set Voltage when Batterie is not full

////LED status////
byte  LED_yellow = 0;                 // 0=Off, 1=blink, 2=on;
byte  LED_blue = 0;
byte  LED_red = 0;
byte  LED_green = 0;
bool  LED_blink_yellow_stat = false;  // Variable to facilitate blining
bool  LED_blink_blue_stat = false;
bool  LED_blink_red_stat = false;
bool  LED_blink_green_stat = false;

////Break and Dumpload status////
int Dumpload=0;                       // 0=OFF, 1=ON;
int Short_Break=0;                    // 0=OFF, 1=ON;

////Motor Control (Motor Steuerung) Variables////
int MS_V1_target=36;                  // Voltage for Motor Start Up
const int MS_DCDC_PWM_0=240;          // starting point for DCDC PWM in start up mode
int MS_DCDC_PWM=240;                  // DCDC PWM in start up mode
int MS_DCDC_PWM_P=2;                  // P-Value for Voltage V1 Control
int MS_DCDC_Delta_PWM;                // Difference to next DCDC PWM Value in start up mode
int MS_RPM=0;                         // RPM Measurement
int MS_RPM_target=150;                // Target Motor RPM in start up mode
int MS_tick = 0;                      // Counter for Motor RPM Measurement
int MS_tick_fin=0;                    // Counter limit for Motor RPM
const int MS_RPM_m_time=1;            // Time of Motor RMP Measurement in seconds
int MS_RPM_frac=75;                   // Amount of signals of 'Signal' PIN of motorcontroller per full motor revolution

////Relay Stauts////
byte Relais_state=0;                  // Relais_state=0 for Generator operation, Relais_state=1 for Motor operation

////wind measurement////
const int wind_m_time = 3;            // Meassuretime in Seconds
int wind_ct = 0;                      // Wind counter
int wind_ct_fin = 0;                  // Wind counter limit
float wind_v1 = 0.0;                  // V1 in m/s
const float wind_v1_factor = 0.66;    // Factor for conversion of V1 into m/s
int wind_status=0;                    // 1: Low, 2:Intermediate, 3: Too high
const int wind_v1_cut_in=3.5;         // Cut in velocity in m/s
float wind_v1_mean=0;                 // mean v1 for windcheck

////Start Up Variables////
String now_st;                        // To store current time as string
unsigned long now;                    // To store current time as numerical value
unsigned long SU_start_time=0;        // To store starting time of Start Up Process
unsigned long SU_step_time=0;         // To store current time of Start Up Process
unsigned long SU_start_time_max=1500; // Maximum time to try to start up the Rotor
int SU_MS=0;                          // Control factor of the Motorcontroller
int SU_MS_stepsize=0;                 // Difference to next Control factor of the Motorcontroller
int SU_MS_P=1;                        // P-Value for MS P_controller
const int SU_stable_tryouts = 6;      // Maximum possible stabily criteria for Motorcontroller
const int SU_Signal_tests=5;          // Test cycles for determing the stabily criteria for Motorcontroller
unsigned int SU_Signal_length[SU_Signal_tests]; // Measuring the length of signals from Motorcontroller
unsigned int SU_Signal_length_min;    // Minimum length of signals from Motorcontroller
unsigned int SU_Signal_length_max;    // Maximum length of signals from Motorcontroller
int SU_stable = 0;                    // Stabily criteria for Motorcontroller (if close to SU_stable_tryouts RPM are measured correctly)
int SU_i=0;                           // Counting variable
float SU_P_1_target= 0;               // Needed power to rotate the Motor at MS_RPM_target
const int SU_P_1_max= 75;             // Maximum tolerated power to rotate the Motor at MS_RPM_target
int SU_Gen_Start_Counter=0;           // Counting when the power to rotate the Motor becomes less: indicator if Turbine has reached motor speed
int SU_finished=0;                    // Indicates if Start Up porcess has finished

////Generator RPM measuring Variables////
int Gen_RPM_frac=26;                  // Multiplier to calculate RPM
int Gen_RPM=0;                        // Indicating Generators RPM
int Gen_RPM_A=0;                      // Indicating Generators previous RPM, needed for MPPT
int Gen_tick = 0;                     // Counter for Interrupt routine
int Gen_tick_fin=0;                   // Maximum Counter for Interrupt routine

////Volatage and Current measuring Variables////
float V_1=0;                          // Voltage V1
float V_2=0;                          // Voltage V2
float V_2_A=0;                        // previous Voltage V2
float I_1=0;                          // Current I1
float I_2=0;                          // Current I2
float I_2_A=0;                        // previous Current I2
float P_1 = 0;                        // Power P1
float P_2 = 0;                        // Power P2
float P_2_A = 0;                      // previous Power P2

////Initialise Analog Digital Converter////
Adafruit_ADS1115 ads;                 // Use this for the 16-bit ADC ADS1115
const int samplelength=20;            // Samplelength for calculating mean value of meaurements
int32_t adc0_mean;                    // mean value of meaurements
int32_t adc1_mean;                    // mean value of meaurements
int32_t adc2_mean;                    // mean value of meaurements
int32_t adc3_mean;                    // mean value of meaurements
int i;                                // Counting variable
int j;                                // Counting variable

////Initialise SD Card////
File dataFile;                        // File on the SD Card
String filename;                      // Filename on the SD Card
String dataString = "";               // Data to store on the SD Card and print on serial monitor

////MPPT Variables////
const int MPPT_wind_v1_epsilon=10;    // if difference in omega is bigger than this, change in v1 is triggered
const int MPPT_delta_DCDC_PWM_0=2;    // Standard difference to next PWM value in MPPT Mode 0
const int MPPT_delta_omega_epsilon=4; // In Mode 1 (waiting) smaller changes are regarded as constant omega
const int MPPT_delta_P_2_epsilon=2;   // In Mode 1 (waiting) smaller changes are regarded as constant P2
const int MPPT_delta_omega_stern_epsilon=8;     // When omega is closer to omega_stern than this value, MPPT switches from fast mode (2) to more precise mode (0)
int MPPT_delta_DCDC_PWM=MPPT_delta_DCDC_PWM_0;  // difference to next PWM value in MPPT
int MPPT_DCDC_PWM=200;                // Current PWM value in MPPT
int MPPT_DCDC_PWM_A=0;                // Previous PWM value in MPPT
float MPPT_omega=0;                   // Current omega in MPPT
float MPPT_omega_stern=0;             // Calculated control variable for MPPT
float MPPT_omega_A=0;                 // Previous omega in MPPT
float MPPT_omega_opt=0;               // Optimum omega in MPPT Mode 2
float MPPT_delta_Omega=0;             // Difference between last and current omega in MPPT
float MPPT_kopt=0;                    // k-factor for MPPT
float MPPT_P_2_opt=0;                 // Optimum power P2 in MPPT Mode 2
float MPPT_delta_P_2=0;               // Difference between last and current P2 in MPPT
float MPPT_delta_P_2_A=0;             // Previous power P2 in MPPT
byte MPPT_delta_wind_v1=0;            // Indicating if velocity v1 has changed due to estimator
byte MPPT_delta_wind_v1_A=0;          // Previous Indicator for wind change
int MPPT_delta_wind_v1_Reason=0;      // Reason wind change has been detected by estimator
byte MPPT_MODE=0;                     // ModeMPPT is in: 0-HCS 1-waiting 2-fast 3- P2 < 0 ->increase load
float MPPT_beta=0.35;                 // P value vor MPPT Mode 2

////CUT OUT VALUES////
const int V_1_cut_out=80;             // Cut out voltage V1
float wind_v1_cut_out=8;              // Cut out wind speed v1
const int Gen_RPM_cut_out=500;        // Cut out generator RPM
const int P_1_cut_out=100;            // Cut out power P2


void setup() {
//// Begin Serial Communication ////
Serial.begin(9600);

//// Initialize DS3231 ////
Serial.println("Initialize DS3231");;
Wire.begin();
Wire.beginTransmission(DS3231_ADDRESSE);
Wire.write(0x0e);                                   // DS3231 Register
Wire.write(B01100011);
Wire.endTransmission();
clock.begin();
//clock.setDateTime(__DATE__, __TIME__);            // Set clock to sketch compiling time: only to set time at first start then remove and compile again
delay(20);

//// SD Card ////
Serial.print("Initializing SD card...");
if (!SD.begin(SD_Card_CS)) {                        // see if the card is present and can be initialized:
Serial.println("Card failed, or not present");    // don't do anything more:
  return;
}
Serial.println("card initialized.");

//// Initialize DS3231 ////
dt = clock.getDateTime();
filename += String(clock.dateFormat("mdHi", dt));
filename += ".txt";

//// SD Card ////
dataFile = SD.open(filename, FILE_WRITE);
if (dataFile) {    // if the file is available, write to it
  dataFile.println(" ");
  Serial.print(filename);
  Serial.println(" open");
} else { // if the file isn't open, pop up an error:
  Serial.print("error opening ");
  Serial.println(filename);
}

//// set up the LCD's number of columns and rows: ////
lcd.begin(20, 4);
lcd.setCursor(0, 0);
lcd.print("Good wind to you!");

//// Define PIN modes ////
pinMode(MS_outputPin, OUTPUT);
pinMode(Relais_FET_PIN, OUTPUT);
pinMode(MS_Sensor_pulsewidth_PIN, INPUT);
pinMode(DCDC_Treiber_SD_Quer, OUTPUT); //SD_Q Sicherheit des MOSFET-Treibers
pinMode(DCDC_PWM_PIN, OUTPUT);
pinMode(Status_LED_yellow, OUTPUT);
pinMode(Status_LED_blue, OUTPUT);
pinMode(Status_LED_red, OUTPUT);
pinMode(Status_LED_green, OUTPUT);
pinMode(Dumpload_FET, OUTPUT);
pinMode(Short_Break_FET, OUTPUT);
pinMode(SU_LED_Pin, OUTPUT);
pinMode(SD_Card_CS, OUTPUT);

//// Set built in clocks ////
TCCR0B = (TCCR0B & 0b11111000) | 0x03;  // Standard
TCCR1B = (TCCR1B & 0b11111000) | 0x01;  // Necessary for PWM @ 32kHz
TCCR2B = (TCCR2B & 0b11111000) | 0x03;  // Standard

//// Set ADC resolution ////  !!!! ADC will be damaged if voltage is out of bounds !!!!
ads.setGain(GAIN_ONE);       const float ADC_faktor = 0.125;  // 1x gain   +/- 4.096V  1 bit = 2mV      0.125mV              6 MOhm
ads.begin();

//// Interrupts ////
attachInterrupt(digitalPinToInterrupt(Gen_PWM_interrupt_PIN), Gen_RPM_count, RISING);   // To measure Generator RPM
attachInterrupt(digitalPinToInterrupt(Sec_interrupt_PIN), Sec_count, RISING);           // Exact Seconds from RTC
attachInterrupt(digitalPinToInterrupt(wind_interrupt_PIN), wind_count, RISING);         // To measure wind speed
attachInterrupt(digitalPinToInterrupt(MS_RPM_interrupt_PIN), MS_RPM_count, RISING);     // To measure Motor RPM

//// Write Data Header on Serial Monitor and SD File ////
Serial.println  ("Year Month Day Hour Minute Second V1 V2 I1 I2 P1 P2 SU_MS SU_Stability MS_RPM Gen_RPM SU_P_1_target SU_Gen_Start_Counter Relais_state wind_v1 wind_v1_mean wind_v1_cut_out wind_status Battery_full MS_DCDC_PWM Dumpload Short_Break MPPT_MODE MPPT_delta_wind_v1 MPPT_delta_wind_v1_Reason MPPT_DCDC_PWM MPPT_omega_stern MPPT_omega_opt MPPT_kopt*10^6 MPPT_P_2_opt MPPT_delta_P_2 MPPT_delta_Omega Codepoint");
dataFile.println("Year Month Day Hour Minute Second V1 V2 I1 I2 P1 P2 SU_MS SU_Stability MS_RPM Gen_RPM SU_P_1_target SU_Gen_Start_Counter Relais_state wind_v1 wind_v1_mean wind_v1_cut_out wind_status Battery_full MS_DCDC_PWM Dumpload Short_Break MPPT_MODE MPPT_delta_wind_v1 MPPT_delta_wind_v1_Reason MPPT_DCDC_PWM MPPT_omega_stern MPPT_omega_opt MPPT_kopt*10^6 MPPT_P_2_opt MPPT_delta_P_2 MPPT_delta_Omega Codepoint");
dataFile.flush();
delay(2000);
}

void loop() {

  Measure();                                          // Measure Data

  Print_data_Serial("1");                             // Print Data to SD Card and Serial Moitor, Datapoint 1

  //  LCD_print();                                      // Print Data LCD Screen

  if (V_2 >= Battery_V2_High) Battery_full = 1;       // Batterie check
  else if (V_2 <= Battery_V2_Low) Battery_full = 0;

  if (Battery_full == 0) {                            // If Batterie is not full

    if (Gen_RPM == 0) {                               // If turbine is not spinning

      while (MS_DCDC_PWM < (MS_DCDC_PWM_0 - 10)) {    // When RPM = 0 set V1 to 12 V by regulating the DCDC PWM to MS_DCDC_PWM_0
        MS_DCDC_PWM = MS_DCDC_PWM + 10;
        analogWrite(DCDC_PWM_PIN, MS_DCDC_PWM);
        delay(500);
      }
      MS_DCDC_PWM = MS_DCDC_PWM_0;
      analogWrite(DCDC_PWM_PIN, MS_DCDC_PWM);

      MPPT_reset();                                   // Reset MPPT values
      clearLED();                                     // Reset LED Status (see interrups tab)
      LED_yellow = 1;                                 // Yellow LED blinking while waiting
      wind_check();                                   // Ceck for windspeed windstatus==1: low wind, 2: intermediate wind, 3: high wind
      Measure();                                      // Measure Data
      Print_data_Serial("2");                         // Print Data to SD Card and Serial Moitor, Datapoint 2
      LCD_print();                                    // Print Data LCD Screen
      switch (wind_status) {
        case 1:                                       // If windstatus==1: low wind
          clearLED();                                   // Reset LED Status (see interrups tab)
          LED_yellow = 1;                               // Yellow LED blinking while waiting
          delay (900000);                               // wait 15 minutes until next windcheck
          break;

        case 2:                                       // If windstatus==2: intermediate wind
          clearLED();                                   // Reset LED Status (see interrups tab)
          LED_green = 1;                                // Green LED blinking while Start Up
          Start_Up();                                   // Start up the rotor
          break;

        case 3:                                       // If windstatus==3: high wind
          clearLED();                                   // Reset LED Status (see interrups tab)
          LED_red = 1;                                  // Red LED blinking while in high winds
          decelerate();                                 // Break down and Block the rotor electrically
          delay (900000);                               // wait 15 minutes until next windcheck
          break;
      }
    }
    else if (Gen_RPM > 0) {                           // If turbine is spinning
      if (wind_v1 >= wind_v1_cut_out ) {            // if windspeed exceeds cut out velocity
        MPPT_reset();                               // Reset MPPT values
        clearLED();                                 // Reset LED Status (see interrups tab)
        LED_red = 1;                                // Red LED blinking while in high winds
        decelerate();                               // Break down and Block the rotor electrically
      } else {
        if (P_1 > P_1_cut_out || V_1 > V_1_cut_out || Gen_RPM > Gen_RPM_cut_out)  {   // check if P1, V1 or Generator RPM exceed limits

          MPPT_reset();                             // Reset MPPT values
          clearLED();                               // Reset LED Status (see interrups tab)
          LED_red = 1;                              // Red LED blinking while in high winds
          wind_v1_cut_out = wind_v1;                // Decrease cut out velocity to current wind speed
          decelerate();                             // Break down and Block the rotor electrically
        } else {                                    // if no limits are exceeded
          clearLED();                               // Reset LED Status (see interrups tab)
          LED_green = 2;                            // Green LED tunred on while in MPPT
          MPPT();                                   // Go one step in MPPT
        }
      }
    }
  } else if (Battery_full == 1) {                     // If the Battery is full
    clearLED();                                       // Reset LED Status (see interrups tab)
    LED_red = 2;                                      // Red LED tunred on while Battery is full -> change Battery
    decelerate();                                     // Break down and Block the rotor electrically
    delay (900000);                                   // Wait 15 minutes to check Battery again
  }
  Print_data_Serial("20");                            // Print Data to SD Card and Serial Moitor, Datapoint 20
}
///////////////////// END OF LOOP ///////////////////////////////////////////////////

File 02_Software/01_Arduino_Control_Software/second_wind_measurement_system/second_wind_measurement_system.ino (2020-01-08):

const int m_time = 3;      //Meassuretime in Seconds
int wind_ct = 0;
float wind = 0.0;
float lambda = 0.0;
unsigned long time = 0;

unsigned long time_a = 0;
unsigned long time_b = 0;
float RPM = 0.0;
unsigned int RPM_a = 0;
unsigned int RPM_ct = 0;
unsigned int RPM_ct_2 = 0;
const int RPM_ct_fin = 1;
const float RPM_fac = float(RPM_ct_fin) * 60 * 1000;
bool  RPM0 = false;

void setup()
{
  Serial.begin(9600);
  time = millis();
  attachInterrupt(digitalPinToInterrupt(2), countRPM, FALLING );
  attachInterrupt(digitalPinToInterrupt(3), countWind, RISING);
  Serial.println  ("n_turb v1 lambda");
}

void loop()
{
  wind_ct = 0;
  delay(1000 * m_time);
  wind = (float)wind_ct / (float)m_time * 0.47;
  lambda = RPM * 2 * 3.141 * 0.75 / (60 * wind);

  if (RPM_ct_2 == RPM_a) {
    Serial.print("0");
    RPM0 = false;
  } else {
    Serial.print(RPM);
    RPM0 = true;
  }
  RPM_a = RPM_ct_2;
  Serial.print(" ");
  Serial.print(wind );       //Speed in m/s
  Serial.print(" ");
  if (RPM0 == false) {
    Serial.println("0");
  } else {
    Serial.println(lambda);
  }
}

void countWind() {
  wind_ct ++;
}

void countRPM() {
  RPM_ct_2 ++;
  time_a = time_b;
  time_b = millis();
  RPM = RPM_fac / float((time_b - time_a));
}

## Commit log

2020-01-08 upload 02_software
    [2019 04 16 20 50 54_all.xlsx, 2019 04 16 20 50 54_all_v2.xlsx]
2020-01-08 upload 03_Construction
    [1593K_Enclosure.kicad_pcb, 1593K_Enclosure.sch, Arduino_As_Uno.kicad_pcb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]
2020-01-09 04_data upload
    [2019 04 16 13 58 24_Ausschnitt.xlsx, 2019 04 16 13 58 24_all.xlsx, 2019 04 16 13 58 24_all_Trennung.xlsx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]
2020-01-09 STL data removal due to LFS disabled
    [Druckteil1_20181128.STL, Druckteil2_20181128.STL, Druckteil3_20181128.STL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]

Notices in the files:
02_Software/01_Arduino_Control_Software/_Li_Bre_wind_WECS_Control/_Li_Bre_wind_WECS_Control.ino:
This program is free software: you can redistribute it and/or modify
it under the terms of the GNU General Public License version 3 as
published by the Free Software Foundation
